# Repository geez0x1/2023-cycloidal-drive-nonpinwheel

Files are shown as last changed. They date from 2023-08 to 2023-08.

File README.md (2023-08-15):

This repository contains Python code and CAD files to (re)create the cycloidal gearing designs, and experiments, from our 2024 paper
_"Experimental comparison of pinwheel and non-pinwheel designs of 3D-printed cycloidal gearing for robotics"_.

Contents:

- Python code to aid in choosing and visualising design parameters, for both pinwheel and non-pinwheel designs
- CAD files of the presented prototypes
- Python code for validation and testing using an ODrive motor controller

Everything is under the MIT license, so feel free to copy and modify as you see fit.

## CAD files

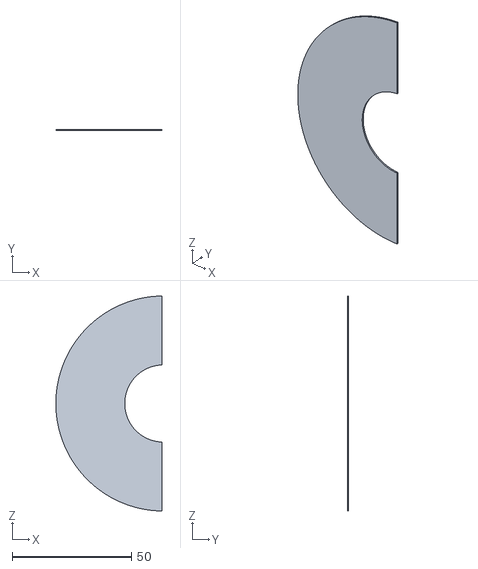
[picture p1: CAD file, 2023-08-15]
mechanical_design/Assembly tools/Input shaft fixture B spacer V2 L.stl
44.5 x 0.6 x 90.0

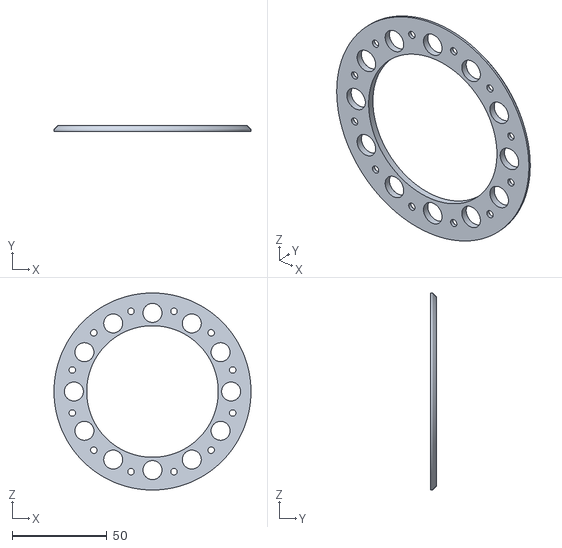
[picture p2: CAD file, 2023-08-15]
mechanical_design/Cycloidal drive main assembly/Cycloidal gearbox/Cycloidal drive housing/Output bearing retaining bracket v14.stl
104.0 x 3.00 x 104.0

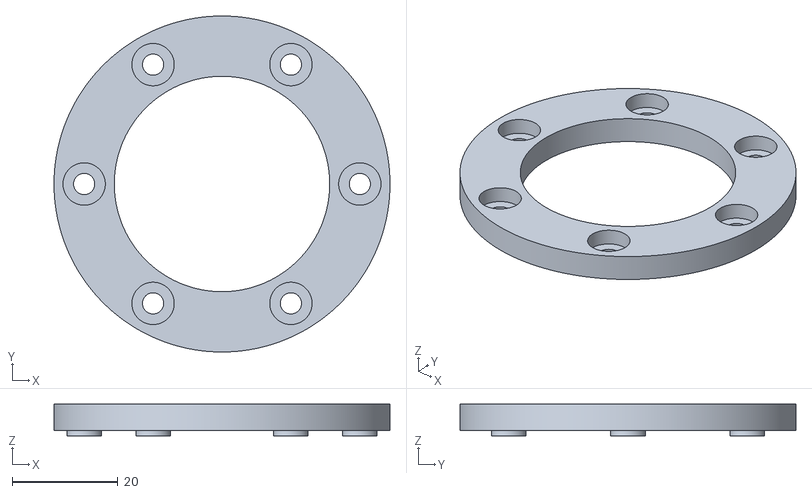
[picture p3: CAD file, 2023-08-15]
mechanical_design/Cycloidal drive main assembly/Cycloidal gearbox/Eccentric shaft assembly/Output shaft stiffness ring v45.stl
63.5 x 63.5 x 6.00

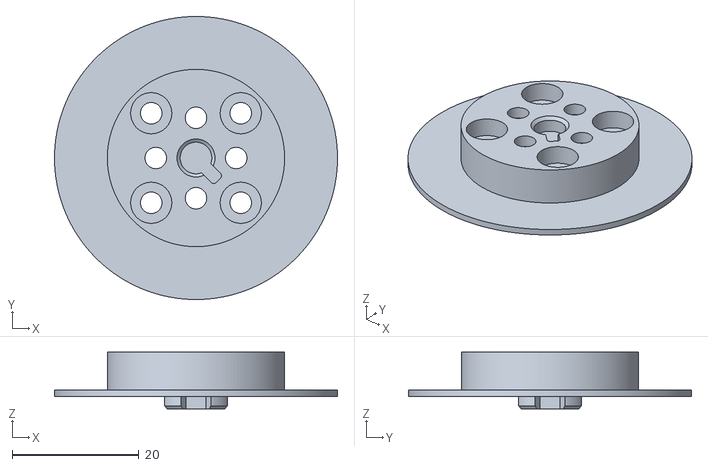
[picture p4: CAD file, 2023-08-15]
mechanical_design/Cycloidal drive main assembly/Motor housing/Motor shaft v65.stl
44.7 x 44.7 x 9.00

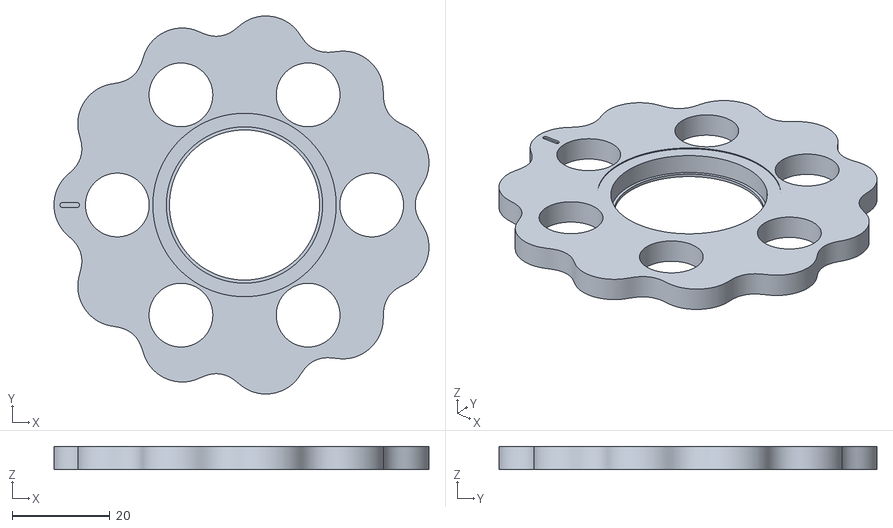
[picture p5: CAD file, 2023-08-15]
mechanical_design/Cycloidal drive main assembly/Cycloidal gearbox/Eccentric shaft assembly/Rotor (R = 4.15 - N = 12 - Rr = 0.45) v83.stl
76.8 x 77.4 x 4.80

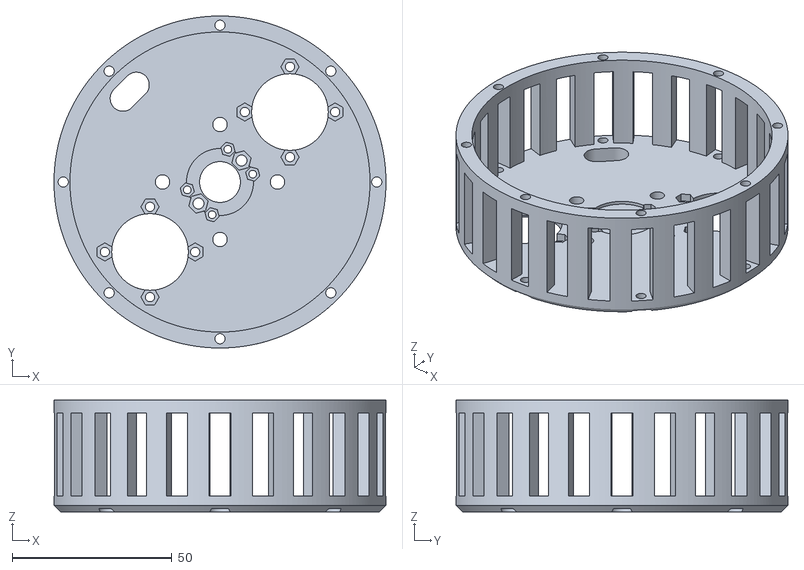
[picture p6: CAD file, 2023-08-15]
mechanical_design/Cycloidal drive main assembly/Motor housing/Motor housing v142.stl
104.0 x 104.0 x 35.0

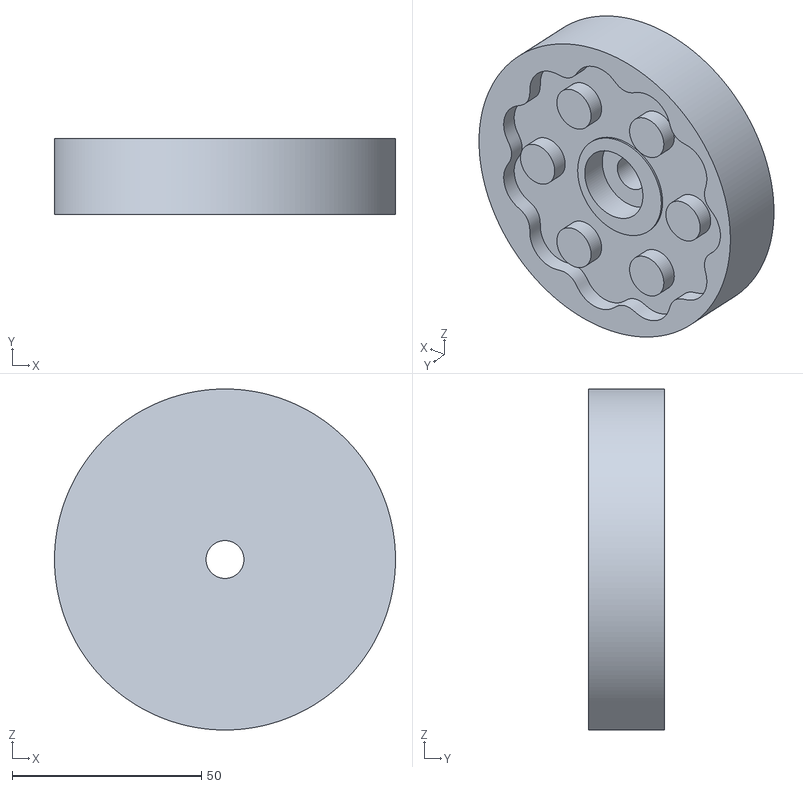
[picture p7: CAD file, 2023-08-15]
mechanical_design/Assembly tools/Input shaft fixture B v13.stl
90.0 x 20.0 x 90.0

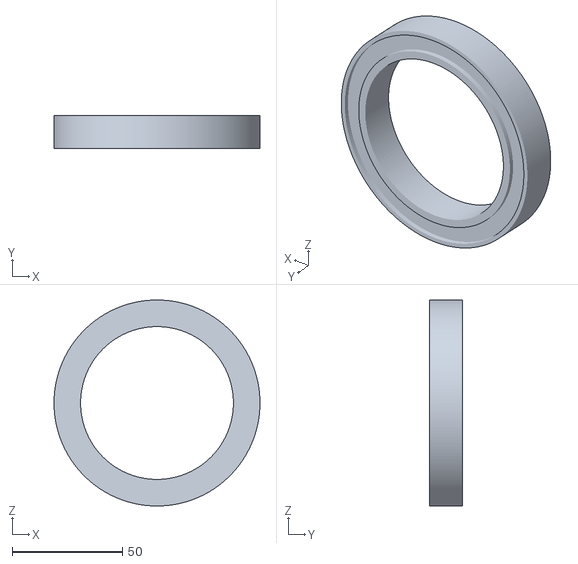
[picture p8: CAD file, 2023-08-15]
mechanical_design/Assembly tools/Bearing support v12.stl
93.6 x 15.0 x 93.6

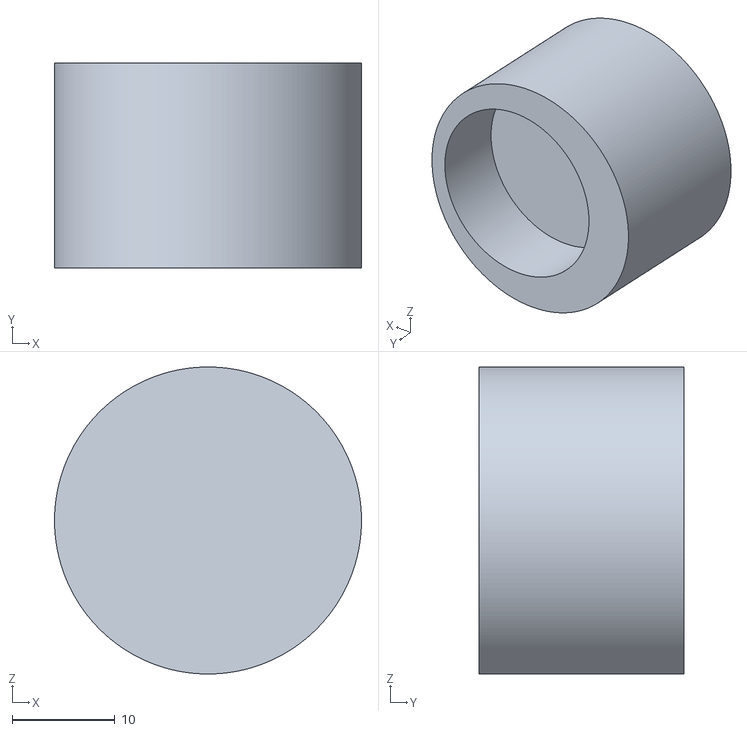
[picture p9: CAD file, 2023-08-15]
mechanical_design/Assembly tools/Press v7.stl
29.9 x 20.0 x 29.9

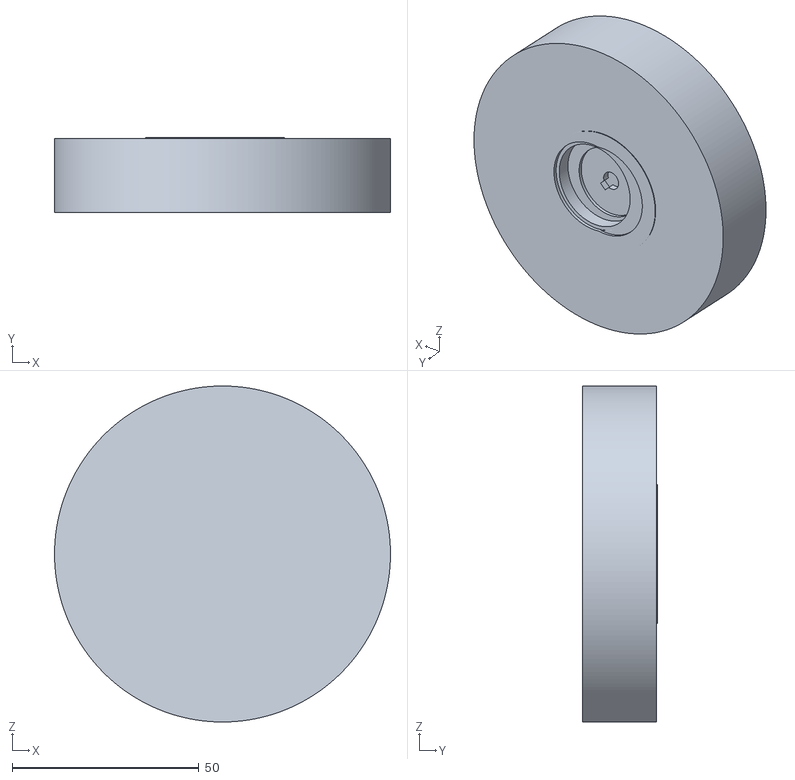
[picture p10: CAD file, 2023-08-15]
mechanical_design/Assembly tools/Input shaft fixture A v13.stl
90.0 x 20.0 x 90.0

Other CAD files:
mechanical_design/Assembly tools/Input shaft fixture B spacer V2 R.stl

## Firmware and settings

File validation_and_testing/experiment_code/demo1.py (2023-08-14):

#!/usr/bin/env python3
# -*- coding: utf-8 -*-
"""
Created on Fri Nov 26 11:14:38 2021

@author: wesley
"""

from __future__ import print_function

import odrive
from odrive.enums import *
import time
import math
import csv
from common import get_output_filename, save_data

# Experiment parameters (pendulum)
def loadInertia():
	m_weights	= 2.0		# Weight plates mass [kg]
	m_bar		= 0.432		# Pendulum mass [kg]
	m_mounting	= 0.211		# Mounting stuff (thread, nuts, etc) [kg]
	L			= 0.5		# Pendulum length

	return (m_weights+m_mounting) * L**2 + (1/3) * m_bar * L**2

# Experiment parameters (LIGHT SHORT pendulum)
def loadInertia_light():
	m_weights	= 0.0		# Weight plates mass [kg]
	m_bar		= (44/50)*0.432 # Pendulum mass [kg]
	m_mounting	= 0			# Mounting stuff (thread, nuts, etc) [kg]
	L			= 0.44		# Pendulum length

	return (m_weights+m_mounting) * L**2 + (1/3) * m_bar * L**2

# Total inertia, scaled to current 
def totalInertia_toCurrent():
	# Load inertia and approximate motor inertia
	I_l = loadInertia_light() / n**2
	I_m = 0.1 * 0.04**2
	
	# Torque constant
	k_t = 0.083
	
	# Return inertia scaled by torque constant (ODrive torque constant=1)
	# Also converted to turns/s^2
	return turns2rad * (I_m + I_l) / k_t


# Demo parameters
sample_time		= 0.02	# Sample time [s] # Limited by USB/UART?
n				= 11	# True gear ratio
turns2deg		= 360	# One turn in [deg]
deg2rad			= math.pi/180 # Degrees to radians
turns2rad		= turns2deg*deg2rad # Turns to rad []
inertia			= totalInertia_toCurrent() # Inertia converted to current

# Motion behaviour
max_speed		= 30	# Max output speed [rad/s]
max_accel		= 140	# Max acceleration/deceleration [rad/s^2]
target_pos		= [math.pi, 1.5*math.pi, 0.5*math.pi, 2*math.pi] # Target positions [rad]
static_time		= 0.00	# How long to stand still between positions [s]
reached_margin	= 0.01	# Acceptable error for reaching setpoint [rad], at output
max_reach_time	= 5.0	# Maximum time allowed to reach the setpoint [s]

# Control gains
pos_gain			= 15*20		# [turns/s / turn] - default 20
vel_gain			= 7*0.16	# [Nm / turns/s] - default 0.16
vel_integrator_gain	= 4*0.32	# [Nm / turn/s^2] - default 0.32
current_lim			= 60		# Current limit [A] (40A tops out at around 31 Nm)
requested_current	= 80		# Current sensing limit [A]
# Not touching current control gains current_gain and
# current_integrator_gain - they are automatically set
# for a given current control bandwidth.

# Prompt user for output filename
out_filename = get_output_filename('out_demo1.csv')

# Find a connected ODrive (this will block until you connect one)
print("Finding odrive..")
my_drive = odrive.find_any()

# First set the reference position to whatever the current position is
input_pos_initial = my_drive.axis0.encoder.pos_estimate
my_drive.axis0.controller.input_pos = input_pos_initial
print('Initial position offset is', round(turns2rad*input_pos_initial/n,2), 'rad.')
print('NOTE: Make sure to start this experiment in a down hanging position!')

# Set encoder and current control bandwidth
my_drive.axis0.encoder.config.bandwidth = 2000
my_drive.axis0.motor.config.current_control_bandwidth = 2000

# Set control mode
# "Trajectory control" - essentially minimum jerk
print('Setting control mode and parameters..')
my_drive.axis0.controller.config.control_mode	= CONTROL_MODE_POSITION_CONTROL
my_drive.axis0.controller.config.input_mode		= INPUT_MODE_TRAP_TRAJ
my_drive.axis0.trap_traj.config.vel_limit		= n * max_speed / turns2rad
my_drive.axis0.trap_traj.config.accel_limit		= n * max_accel / turns2rad
my_drive.axis0.trap_traj.config.decel_limit		= n * max_accel / turns2rad
my_drive.axis0.controller.config.inertia		= inertia

# Set control gains
my_drive.axis0.controller.config.pos_gain = pos_gain
my_drive.axis0.controller.config.vel_gain = vel_gain
my_drive.axis0.controller.config.vel_integrator_gain = vel_integrator_gain

# Set current limit
#my_drive.axis0.motor.config.current_lim = current_lim
#my_drive.axis0.motor.config.requested_current_range = requested_current

print('Starting closed loop control..')
my_drive.axis0.requested_state = AXIS_STATE_CLOSED_LOOP_CONTROL
time.sleep(1.0)

# Record data
print('Recording data..')
data = []
t0 = time.monotonic()

# Iterator through target positions
motion_it = 0
motion_setpoint_reached = True
t_motion_setpoint_reached = t0

# Until we break..
while True:
	# Get iteration start time
	t = time.monotonic()

	# Get data
	motorPos    = my_drive.axis0.encoder.pos_estimate
	outputPos   = 0#my_drive.axis1.encoder.pos_estimate # Encoder not available, and not really needed
	motorVel    = my_drive.axis0.encoder.vel_estimate
	outputVel   = 0#my_drive.axis1.encoder.vel_estimate # Encoder not available, and not really needed
	Iq_set		= my_drive.axis0.motor.current_control.Iq_setpoint
	Iq_meas		= my_drive.axis0.motor.current_control.Iq_measured
	data.append([
		t-t0,
		motorPos,
		outputPos,
		motorVel,
		outputVel,
		my_drive.axis0.controller.input_pos,
		Iq_set,
		Iq_meas,
	])

	# Check if we have reached the setpoint
	# Compute error in [rad], at the output
	if not motion_setpoint_reached:
		e = turns2rad * (my_drive.axis0.controller.input_pos - motorPos) / n
		if math.fabs(e) <= reached_margin:
			t_motion_setpoint_reached = time.monotonic()
			motion_setpoint_reached = True # Don't keep updating the reached time
			print('Setpoint reached.')
		elif time.monotonic() - t_motion_setpoint_reached > max_reach_time:
			print('Failed to reach setpoint, aborting...')
			break

	# If there has been more time than `static_time` since we reached the setpoint, let's go
	if motion_setpoint_reached and time.monotonic() - t_motion_setpoint_reached >= static_time:
		# Check whether we have reached all set points, and then the starting position
		if motion_it >= len(target_pos)+1:
			# If we have reached the starting position, we can stop
			break
		elif motion_it >= len(target_pos):
			# If we have reached all target positions, we go to the starting position
			target_pos_motor = input_pos_initial
		else:
			# Otherwise we go to the next target position
			target_pos_motor = input_pos_initial + n * target_pos[motion_it] / turns2rad # Motor pos in [turns]

		print('Updating set point to', round(target_pos_motor*turns2rad/n,2), 'rad..')

		# Set new set point
		my_drive.axis0.controller.input_pos = target_pos_motor

		# Update iterator for setpoints so we set the next one next time
		motion_it += 1

		# We have not reached the new setpoint yet
		motion_setpoint_reached = False

	# Sleep for loop
	try:
		time.sleep(sample_time - (time.monotonic()-t))
	except:
		print('    WARNING: Iteration took longer than sample time of', sample_time, 's')

# Stop motor
# TODO CAN WE REMOVE THIS?
print('Finished, again setting initial position (should be no move, in which case remove this)..')
my_drive.axis0.controller.input_pos = input_pos_initial
time.sleep(1)

# Stop controller
print('Stopping closed-loop control..')
my_drive.axis0.requested_state = AXIS_STATE_IDLE

# Save data
save_data(data, out_filename)

# End
print('Done.')

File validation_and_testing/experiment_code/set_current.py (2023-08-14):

#!/usr/bin/env python3
# -*- coding: utf-8 -*-
"""
Created on Fri Nov 26 11:14:38 2021

@author: wesley
"""

from __future__ import print_function

import odrive
from odrive.enums import *
import time
import math
import csv
import curses
import sys
from common import get_output_filename, save_data, append_filename

def main(stdscr):
	# Test parameters
	sample_time		= 0.02	# Sample time [s] # Limited by USB/UART?
	n				= 11	# Gear ratio []
	amp_per_step	= 0.1	# Ampere to increment per step
	turns2deg		= 360	# One turn in degrees []
	deg2rad			= math.pi/180 # Degrees to radians []
	turns2rad		= turns2deg*deg2rad # Turns to rad []

	# Control gains
	# Not setting gains as we are setting current directly in this test
	#current_lim			= 40		# Current limit [A] (40A tops out at around 31 Nm)
	#requested_current	= 60		# Current sensing limit [A]

	# Prompt user for output filename
	out_filename = get_output_filename('out_set_current.csv', stdscr)

	# curses: disable echo
	curses.noecho()
	# curses: make getch() non-blocking
	stdscr.nodelay(1)
	line = 0

	# Find a connected ODrive (this will block until you connect one)
	stdscr.addstr(line,0,'Finding odrive..'); line += 1
	my_drive = odrive.find_any()
	
	# Check if the torque constant is unity (otherwise the setpoint is not current)
	if my_drive.axis0.motor.config.torque_constant != 1.0:
		curses.endwin()
		sys.exit('torque_constant is not 1.0: Cannot continue. Quitting.')

	# Set control mode
	# Torque control (= current control)
	stdscr.addstr(line,0,'Setting control mode and parameters..'); line += 1
	my_drive.axis0.controller.config.control_mode = CONTROL_MODE_TORQUE_CONTROL
	my_drive.axis0.controller.config.input_mode = INPUT_MODE_PASSTHROUGH
	my_drive.axis0.controller.config.enable_torque_mode_vel_limit = False # This function will cause issues if vel_gain is zero, and is weird anyway.
	
	# Set current limit
	#my_drive.axis0.motor.config.current_lim = current_lim
	#my_drive.axis0.motor.config.requested_current_range = requested_current

	# Then start position control
	stdscr.addstr(line,0,'Starting closed loop control..'); line += 1
	my_drive.axis0.requested_state = AXIS_STATE_CLOSED_LOOP_CONTROL
	time.sleep(1.0)

	# Record data
	stdscr.addstr(line,0,'Recording data..'); line += 1
	data = []
	data_stiffness = []
	t0 = time.monotonic()
	
	# Set initial current setpoint (KEEP ZERO)
	current_setpoint = 0

	# Loop until told to stop
	line += 1; stdscr.addstr(line,0,'Use +/- to increase/decrease current, or press \'q\' to stop.'); line += 1; line += 1
	stdscr.addstr(line,4,'Current setpoint: '+str(current_setpoint)+' A..')
	while True:
		# Get iteration start time
		t = time.monotonic()
		
		# curses: get keyboard input, returns -1 if none available
		c = stdscr.getch()

		if c == ord('+') or c == ord('='):
			current_setpoint += amp_per_step
			my_drive.axis0.controller.input_torque = current_setpoint
			stdscr.addstr(line,4,'Current setpoint: '+str(current_setpoint)+' A..')

		elif c == ord('-'):
			current_setpoint -= amp_per_step
			my_drive.axis0.controller.input_torque = current_setpoint
			stdscr.addstr(line,4,'Current setpoint: '+str(current_setpoint)+' A..')

		elif c == ord('q'):
			line += 1
			break

		# Get data
		motorPos	= my_drive.axis0.encoder.pos_estimate
		outputPos	= my_drive.axis1.encoder.pos_estimate # May or may not be available
		motorVel	= my_drive.axis0.encoder.vel_estimate
		outputVel	= my_drive.axis1.encoder.vel_estimate # May or may not be available
		Iq_set		= my_drive.axis0.motor.current_control.Iq_setpoint
		Iq_meas		= my_drive.axis0.motor.current_control.Iq_measured
		data.append([
			t-t0,
			motorPos,
			outputPos,
			motorVel,
			outputVel,
			current_setpoint,
			Iq_set,
			Iq_meas,
		])
		
		# Sleep for loop
		try:
			time.sleep(sample_time - (time.monotonic()-t))
		except:
			print('    WARNING: Iteration took longer than sample time of', sample_time, 's')

	# Stop controller
	line += 1; stdscr.addstr(line,0,'Finished, stopping closed-loop control..'); line += 1
	my_drive.axis0.controller.input_torque = 0
	my_drive.axis0.requested_state = AXIS_STATE_IDLE
	c = stdscr.getch()
	time.sleep(1)

	# Stop curses window
	curses.endwin()

	# Save data
	save_data(data, out_filename)

	# End
	print('Done.')


# Run
if __name__ == '__main__':
	curses.wrapper(main)

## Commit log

2023-08-14 Adding validation and testing tools (Python, using ODrive motor controller)
2023-08-15 Committing CAD files
    [Bearing support v12.stl, Input shaft fixture A v13.stl, Input shaft fixture B spacer V2 L.stl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]
